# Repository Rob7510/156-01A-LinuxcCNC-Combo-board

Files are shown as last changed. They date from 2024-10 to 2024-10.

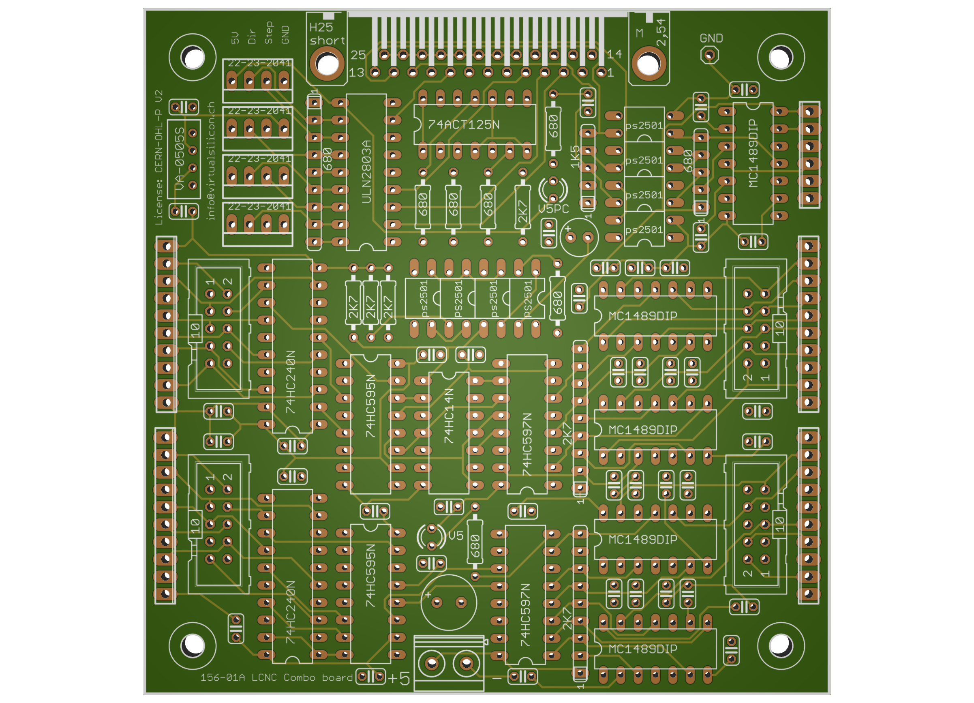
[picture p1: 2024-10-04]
image.png

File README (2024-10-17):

Note: First version, in test.

This board can drive in LinuxCNC a 3-axis CNC over a single printer port set to default(out/epp) mode,
and provides 4 (pin 10-13) + 16 signal inputs and 9 (pin 1-9) + 16 output signals using the integrated
LSRIO16 softwaare multiplexer.

The X, Y, Z axis and A (or two other signals instead of A) are not isolated from the PC,
they connect to stepper drivers that are normally floating.
The remaining 20 input and 16 output signals are electrically isolated from the PC.

Combo port example configuration:

Pin Output Signal
1   Enable
2   X step
3   X dir
4   Y step
5   Y dir
6   Z step
7   Z dir
8   Spindle  etc
9   Aux out
14  LSRIO16 output (fixed onboard)
16  LSRIO16 clock (fixed onboard)
17  LSRIO16 data latch (fixed onboard)

Pin Input signal
10  X home
11  Y home
12  Z home
13  Probe
15  LSRIO16 input (fixed onboard)

All other signals (eg limits, ext_estop, buttons, lights) can be handled by the 16 in and 16
output signals of the LSRIO16 multimplexer with a polling delay of max 300 msec.

LSRIO16 fixed signal connections 
RCLK   <- SRIO-DATA_LATCH (P17)
SRCLK  <- SRIO-CLOCK-OUTPUT (P16)
DT-OUT -> LSRIO-INPUT-STREAM (P15)
DT-IN  <- SRIO-OUTPUT-STREAM (P14)
SRLD = inverted RCLK

Test software to set outputs and read inputs: mx16_test.hal, mx16_test.xml

updated 2024-10-17

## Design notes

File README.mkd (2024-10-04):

This board is desiged to build a simple 3-axis CNC with this single 'combo' adapter.
The integrated LCNC LSRIO16 provides an additional 16 input and 16 output ports

The X, Y, Z axis and A or two other signals are not isolated, as they connect to stepper drivers.
The remainder of all I/O signals is electrically isolated from the PC.

Combo port example configuration:

Pin Output Signal
1   Enable
2   X step
3   X dir
4   Y step
5   Y dir
6   Z step
7   Z dir
8   Spindle  etc
9   Aux out
14  LSRIO16 output
16  LSRIO16 clock
17  LSRIO16 data latch

Pin Input signal
10  X home
11  Y home
12  Z home
13  Probe
15  LSRIO16 input

All other signals (limits, ext_estop)
can be handled by the 16 in and 16
output signals of the mux. (Polling
delay max 300 msec)

RCLK   <- SRIO-DATA_LATCH (P17)
SRCLK  <- SRIO-CLOCK-OUTPUT (P16)
DT-OUT -> LSRIO-INPUT-STREAM (P15)
DT-IN  <- SRIO-OUTPUT-STREAM (P14)
SRLD = inverted RCLK

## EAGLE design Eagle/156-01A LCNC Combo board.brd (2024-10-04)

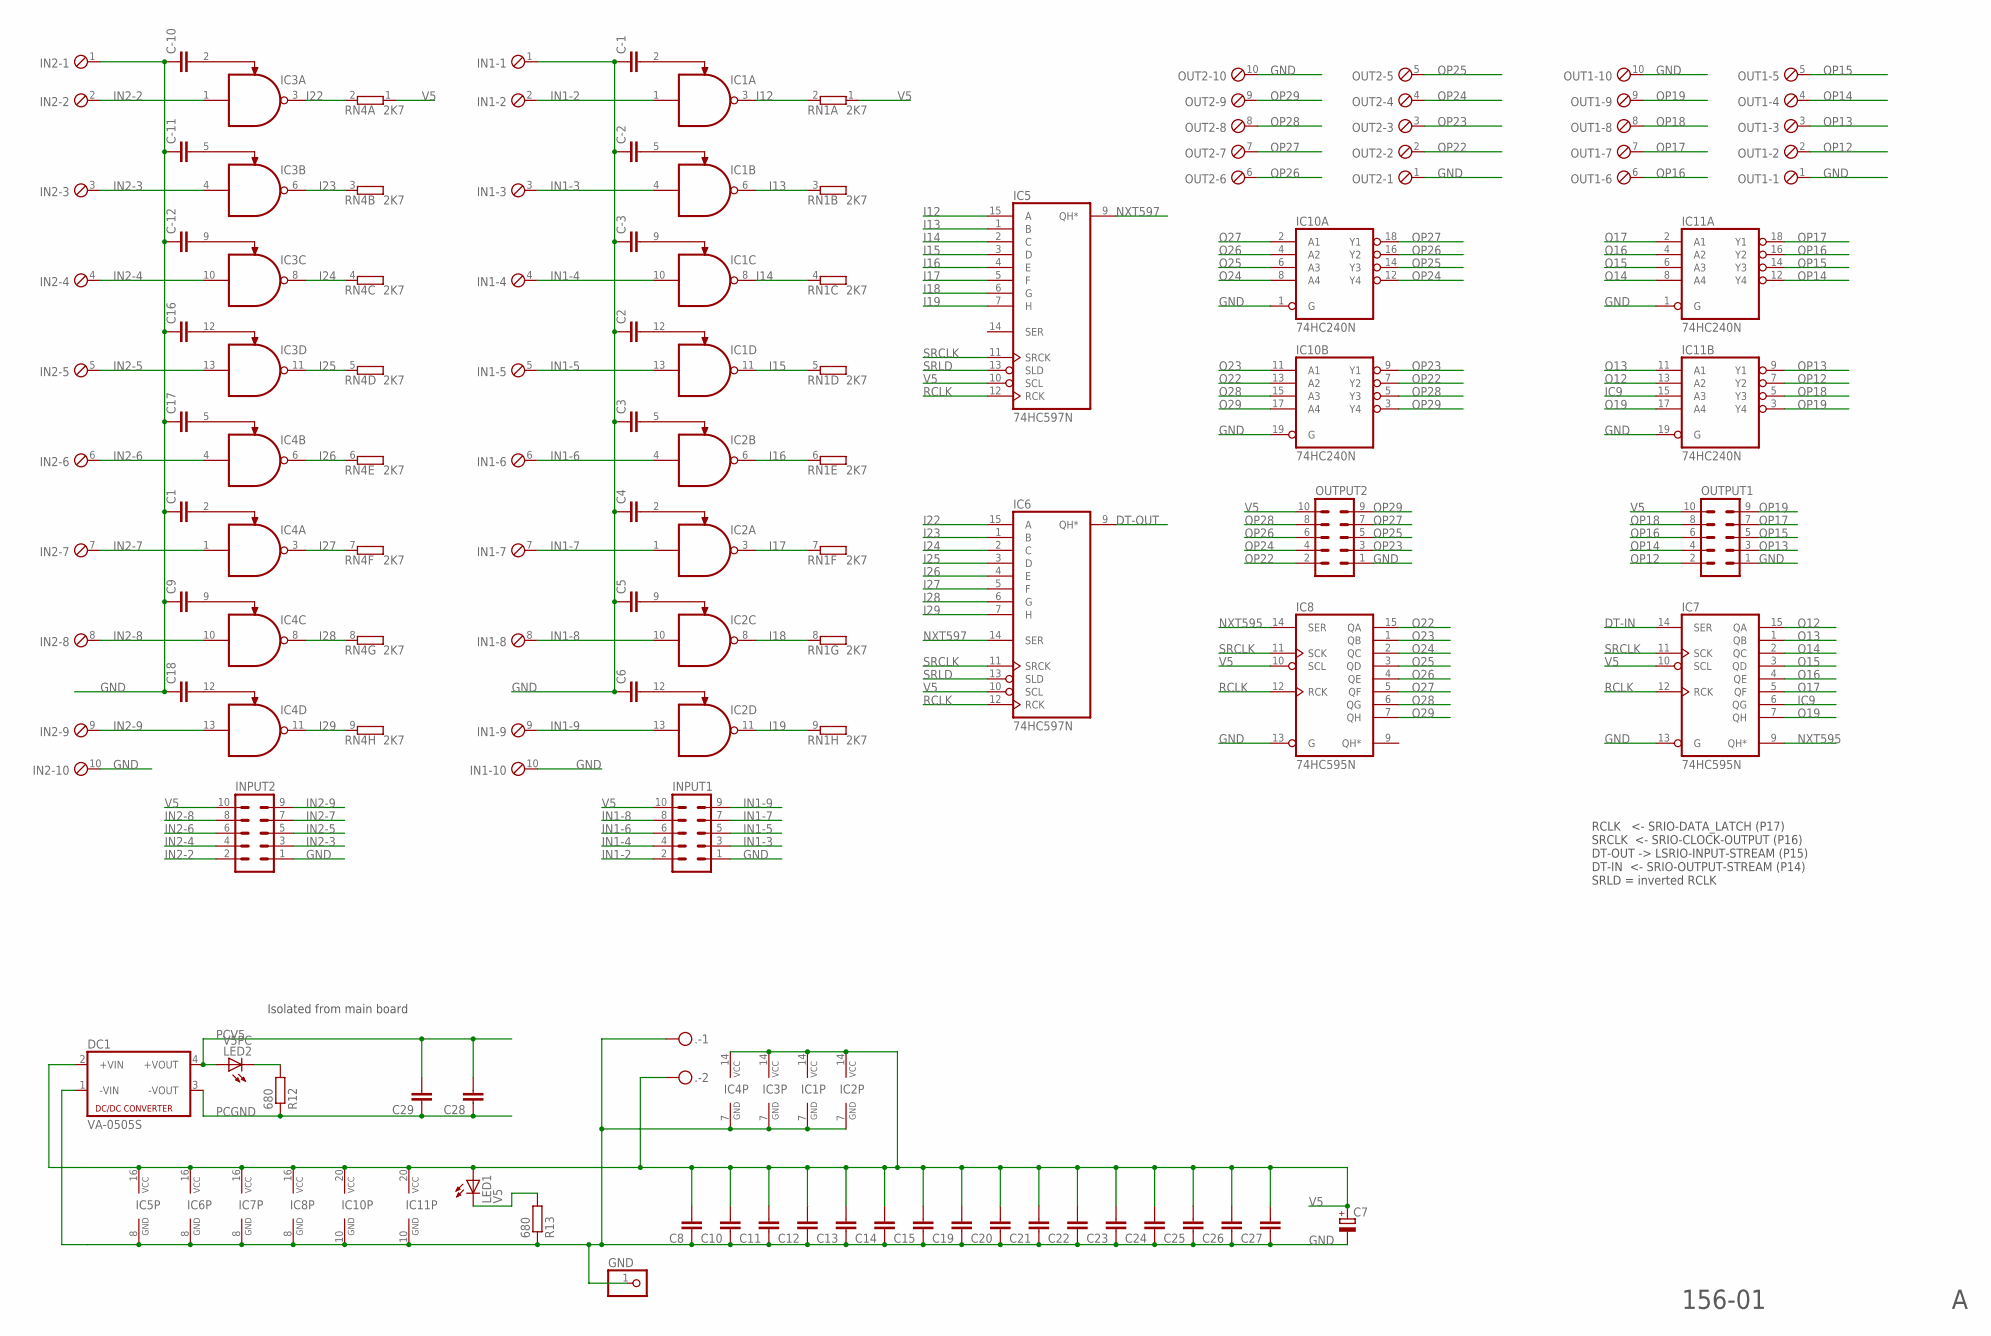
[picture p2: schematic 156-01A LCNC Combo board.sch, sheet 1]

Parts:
.: MKDSN1,5/2-5,08
C1, C2, C3, C4, C5, C6, C8, C9, C10, C11, C12, C13, C14, C15, C16, C17, C18, C19, C20, C21, C22, C23, C24, C25, C26, C27, C28, C29: C-EU025-024X044; C025-024X044
C7: CPOL-EUE3.5-8; E3,5-8
C-1, C-2, C-3, C-10, C-11, C-12: C-EU025-024X044; C025-024X044
DC1: VA-0505S; 4SIL
GND: PINHD-1X1; 1X01
IC1, IC2, IC3, IC4: MC1489DIP; DIL14
IC5, IC6: 74HC597N; DIL16
IC7, IC8: 74HC595N; DIL16
IC10, IC11: 74HC240N; DIL20
IN1, IN2: MPT10; 10POL254
INPUT1, INPUT2: ML10
LED1: V5; LED3MM
LED2: V5PC; LED3MM
OUT1, OUT2: MPT10; 10POL254
OUTPUT1, OUTPUT2: ML10
R12, R13: 680; 0207/10
RN1, RN4: 2K7; SIL9

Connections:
DT-IN: IC7.14 (SER); also elsewhere on the board
DT-OUT: IC6.9 (QH*); also elsewhere on the board
GND: ..1, C1.1, C2.1, C3.1, C4.1, C5.1, C6.1, C7.-, C8.1, C9.1, C10.1, C11.1, C12.1, C13.1, C14.1, C15.1, C16.1, C17.1, C18.1, C19.1, C20.1, C21.1, C22.1, C23.1, C24.1, C25.1, C26.1, C27.1, C-1.1, C-2.1, C-3.1, C-10.1, C-11.1, C-12.1, DC1.1 (-VIN), GND.1, IC1.7 (GND), IC2.7 (GND), IC3.7 (GND), IC4.7 (GND), IC5.8 (GND), IC6.8 (GND), IC7.8 (GND), IC7.13 (G), IC8.8 (GND), IC8.13 (G), IC10.1 (G), IC10.10 (GND), IC10.19 (G), IC11.1 (G), IC11.10 (GND), IC11.19 (G), IN1.1, IN1.10, IN2.1, IN2.10, INPUT1.1, INPUT2.1, OUT1.1, OUT1.10, OUT2.1, OUT2.10, OUTPUT1.1, OUTPUT2.1, R13.1; also elsewhere on the board
I12: IC1.3 (O), IC5.15 (A), RN1.2
I13: IC1.6 (O), IC5.1 (B), RN1.3 (2)
I14: IC1.8 (O), IC5.2 (C), RN1.4 (2)
I15: IC1.11 (O), IC5.3 (D), RN1.5 (2)
I16: IC2.6 (O), IC5.4 (E), RN1.6 (2)
I17: IC2.3 (O), IC5.5 (F), RN1.7 (2)
I18: IC2.8 (O), IC5.6 (G), RN1.8 (2)
I19: IC2.11 (O), IC5.7 (H), RN1.9 (2)
I22: IC3.3 (O), IC6.15 (A), RN4.2
I23: IC3.6 (O), IC6.1 (B), RN4.3 (2)
I24: IC3.8 (O), IC6.2 (C), RN4.4 (2)
I25: IC3.11 (O), IC6.3 (D), RN4.5 (2)
I26: IC4.6 (O), IC6.4 (E), RN4.6 (2)
I27: IC4.3 (O), IC6.5 (F), RN4.7 (2)
I28: IC4.8 (O), IC6.6 (G), RN4.8 (2)
I29: IC4.11 (O), IC6.7 (H), RN4.9 (2)
IC9: IC7.6 (QG), IC11.15 (A3)
IN1-2: IC1.1 (I0), IN1.2, INPUT1.2
IN1-3: IC1.4 (I0), IN1.3, INPUT1.3
IN1-4: IC1.10 (I0), IN1.4, INPUT1.4
IN1-5: IC1.13 (I0), IN1.5, INPUT1.5
IN1-6: IC2.4 (I0), IN1.6, INPUT1.6
IN1-7: IC2.1 (I0), IN1.7, INPUT1.7
IN1-8: IC2.10 (I0), IN1.8, INPUT1.8
IN1-9: IC2.13 (I0), IN1.9, INPUT1.9
IN2-2: IC3.1 (I0), IN2.2, INPUT2.2
IN2-3: IC3.4 (I0), IN2.3, INPUT2.3
IN2-4: IC3.10 (I0), IN2.4, INPUT2.4
IN2-5: IC3.13 (I0), IN2.5, INPUT2.5
IN2-6: IC4.4 (I0), IN2.6, INPUT2.6
IN2-7: IC4.1 (I0), IN2.7, INPUT2.7
IN2-8: IC4.10 (I0), IN2.8, INPUT2.8
IN2-9: IC4.13 (I0), IN2.9, INPUT2.9
unnamed: C-2.2, IC1.5 (I1)
unnamed: C-10.2, IC3.2 (I1)
unnamed: C17.2, IC4.5 (I1)
unnamed: C-3.2, IC1.9 (I1)
unnamed: C1.2, IC4.2 (I1)
unnamed: C9.2, IC4.9 (I1)
unnamed: C18.2, IC4.12 (I1)
unnamed: C2.2, IC1.12 (I1)
unnamed: C4.2, IC2.2 (I1)
unnamed: C5.2, IC2.9 (I1)
unnamed: C6.2, IC2.12 (I1)
unnamed: C-1.2, IC1.2 (I1)
unnamed: C3.2, IC2.5 (I1)
unnamed: LED2.K (C), R12.2
unnamed: LED1.K (C), R13.2
unnamed: C-11.2, IC3.5 (I1)
unnamed: C-12.2, IC3.9 (I1)
unnamed: C16.2, IC3.12 (I1)
NXT595: IC7.9 (QH*), IC8.14 (SER)
NXT597: IC5.9 (QH*), IC6.14 (SER)
O12: IC7.15 (QA), IC11.13 (A2)
O13: IC7.1 (QB), IC11.11 (A1)
O14: IC7.2 (QC), IC11.8 (A4)
O15: IC7.3 (QD), IC11.6 (A3)
O16: IC7.4 (QE), IC11.4 (A2)
O17: IC7.5 (QF), IC11.2 (A1)
O19: IC7.7 (QH), IC11.17 (A4)
O22: IC8.15 (QA), IC10.13 (A2)
O23: IC8.1 (QB), IC10.11 (A1)
O24: IC8.2 (QC), IC10.8 (A4)
O25: IC8.3 (QD), IC10.6 (A3)
O26: IC8.4 (QE), IC10.4 (A2)
O27: IC8.5 (QF), IC10.2 (A1)
O28: IC8.6 (QG), IC10.15 (A3)
O29: IC8.7 (QH), IC10.17 (A4)
OP12: IC11.7 (Y2), OUT1.2, OUTPUT1.2
OP13: IC11.9 (Y1), OUT1.3, OUTPUT1.3
OP14: IC11.12 (Y4), OUT1.4, OUTPUT1.4
OP15: IC11.14 (Y3), OUT1.5, OUTPUT1.5
OP16: IC11.16 (Y2), OUT1.6, OUTPUT1.6
OP17: IC11.18 (Y1), OUT1.7, OUTPUT1.7
OP18: IC11.5 (Y3), OUT1.8, OUTPUT1.8
OP19: IC11.3 (Y4), OUT1.9, OUTPUT1.9
OP22: IC10.7 (Y2), OUT2.2, OUTPUT2.2
OP23: IC10.9 (Y1), OUT2.3, OUTPUT2.3
OP24: IC10.12 (Y4), OUT2.4, OUTPUT2.4
OP25: IC10.14 (Y3), OUT2.5, OUTPUT2.5
OP26: IC10.16 (Y2), OUT2.6, OUTPUT2.6
OP27: IC10.18 (Y1), OUT2.7, OUTPUT2.7
OP28: IC10.5 (Y3), OUT2.8, OUTPUT2.8
OP29: IC10.3 (Y4), OUT2.9, OUTPUT2.9
PCGND: C28.1, C29.1, DC1.3 (-VOUT), R12.1; also elsewhere on the board
PCV5: C28.2, C29.2, DC1.4 (+VOUT), LED2.A; also elsewhere on the board
RCLK: IC5.12 (RCK), IC6.12 (RCK), IC7.12 (RCK), IC8.12 (RCK); also elsewhere on the board
SRCLK: IC5.11 (SRCK), IC6.11 (SRCK), IC7.11 (SCK), IC8.11 (SCK); also elsewhere on the board
SRLD: IC5.13 (SLD), IC6.13 (SLD); also elsewhere on the board
V5: ..2, C7.+, C8.2, C10.2, C11.2, C12.2, C13.2, C14.2, C15.2, C19.2, C20.2, C21.2, C22.2, C23.2, C24.2, C25.2, C26.2, C27.2, DC1.2 (+VIN), IC1.14 (VCC), IC2.14 (VCC), IC3.14 (VCC), IC4.14 (VCC), IC5.10 (SCL), IC5.16 (VCC), IC6.10 (SCL), IC6.16 (VCC), IC7.10 (SCL), IC7.16 (VCC), IC8.10 (SCL), IC8.16 (VCC), IC10.20 (VCC), IC11.20 (VCC), INPUT1.10, INPUT2.10, LED1.A, OUTPUT1.10, OUTPUT2.10, RN1.1, RN4.1; also elsewhere on the board

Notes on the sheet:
Isolated from main board
RCLK <- SRIO-DATA_LATCH (P17) SRCLK <- SRIO-CLOCK-OUTPUT (P16) DT-OUT -> LSRIO-INPUT-STREAM (P15) DT-IN <- SRIO-OUTPUT-STREAM (P14) SRLD = inverted RCLK
156-01

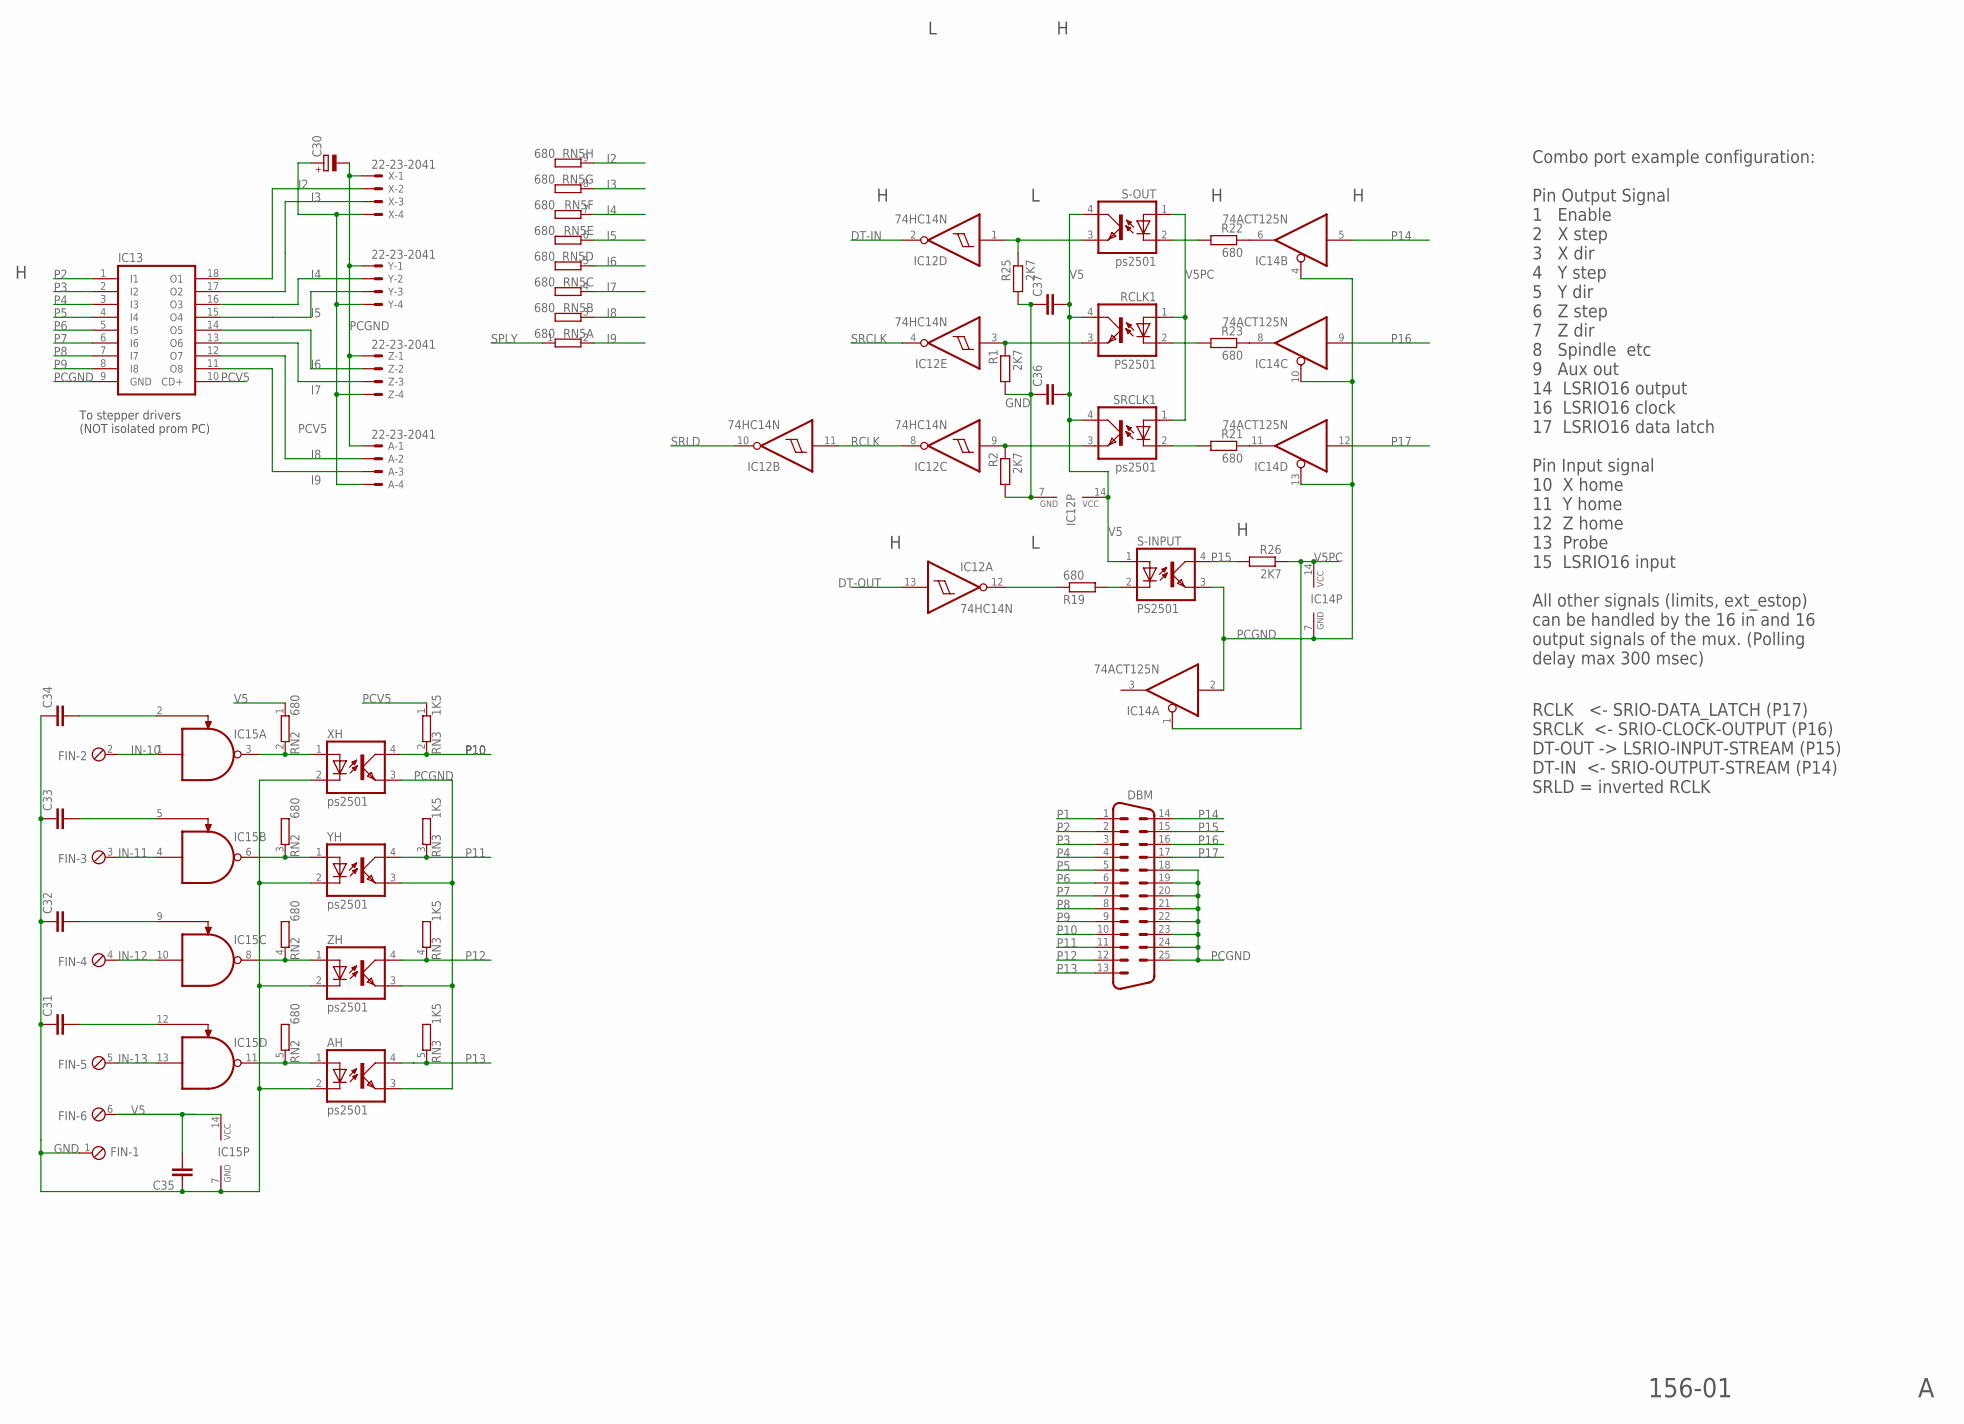
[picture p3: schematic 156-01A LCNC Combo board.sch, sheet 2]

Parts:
A: 22-23-2041
AH: ps2501; DIL04
C30: CPOL-EUE2.5-6; E2,5-6
C31, C32, C33, C34, C35, C36, C37: C-EU025-024X044; C025-024X044
DBM: M25HP
FIN: MPT6; 6POL254
IC12: 74HC14N; DIL14
IC13: ULN2803A; DIL18
IC14: 74ACT125N; DIL14
IC15: MC1489DIP; DIL14
R1, R2, R25, R26: 2K7; 0207/10
R19, R21, R22, R23: 680; 0207/10
RCLK1: PS2501; DIL04
RN2: 680; SIL5
RN3: 1K5; SIL5
RN5: 680; SIL9
S-INPUT: PS2501; DIL04
S-OUT: ps2501; DIL04
SRCLK1: ps2501; DIL04
X: 22-23-2041
XH: ps2501; DIL04
Y: 22-23-2041
YH: ps2501; DIL04
Z: 22-23-2041
ZH: ps2501; DIL04

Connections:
DT-IN: IC12.2 (O); also elsewhere on the board
DT-OUT: IC12.13 (I); also elsewhere on the board
GND: AH.2 (C), C31.1, C32.1, C33.1, C34.1, C35.1, C36.1, C37.1, FIN.1, IC12.7 (GND), IC15.7 (GND), R1.2, R2.2, R25.2, XH.2 (C), YH.2 (C), ZH.2 (C); also elsewhere on the board
I2: IC13.18 (O1), RN5.9 (2), X.2
I3: IC13.17 (O2), RN5.8 (2), X.3
I4: IC13.16 (O3), RN5.7 (2), Y.2
I5: IC13.15 (O4), RN5.6 (2), Y.3
I6: IC13.14 (O5), RN5.5 (2), Z.2
I7: IC13.13 (O6), RN5.4 (2), Z.3
I8: A.2, IC13.12 (O7), RN5.3 (2)
I9: A.3, IC13.11 (O8), RN5.2
IN-10: FIN.2, IC15.1 (I0)
IN-11: FIN.3, IC15.4 (I0)
IN-12: FIN.4, IC15.10 (I0)
IN-13: FIN.5, IC15.13 (I0)
unnamed: IC15.3 (O), RN2.2, XH.1 (A)
unnamed: IC14.6 (O), R22.1
unnamed: IC15.8 (O), RN2.4 (2), ZH.1 (A)
unnamed: AH.1 (A), IC15.11 (O), RN2.5 (2)
unnamed: C33.2, IC15.5 (I1)
unnamed: C34.2, IC15.2 (I1)
unnamed: C32.2, IC15.9 (I1)
unnamed: C31.2, IC15.12 (I1)
unnamed: IC15.6 (O), RN2.3 (2), YH.1 (A)
unnamed: R22.2, S-OUT.2 (C)
unnamed: IC12.3 (I), R1.1, RCLK1.3 (EMIT)
unnamed: R23.2, RCLK1.2 (C)
unnamed: IC12.1 (I), R25.1, S-OUT.3 (EMIT)
unnamed: IC12.9 (I), R2.1, SRCLK1.3 (EMIT)
unnamed: R21.2, SRCLK1.2 (C)
unnamed: IC12.12 (O), R19.1
unnamed: IC14.11 (O), R21.1
unnamed: IC14.8 (O), R23.1
unnamed: R19.2, S-INPUT.2 (C)
P1: DBM.1
P2: DBM.2, IC13.1 (I1)
P3: DBM.3, IC13.2 (I2)
P4: DBM.4, IC13.3 (I3)
P5: DBM.5, IC13.4 (I4)
P6: DBM.6, IC13.5 (I5)
P7: DBM.7, IC13.6 (I6)
P8: DBM.8, IC13.7 (I7)
P9: DBM.9, IC13.8 (I8)
P10: DBM.10, RN3.2, XH.4 (COL)
P11: DBM.11, RN3.3 (2), YH.4 (COL)
P12: DBM.12, RN3.4 (2), ZH.4 (COL)
P13: AH.4 (COL), DBM.13, RN3.5 (2)
P14: DBM.14, IC14.5 (I)
P15: DBM.15, R26.2, S-INPUT.4 (COL)
P16: DBM.16, IC14.9 (I)
P17: DBM.17, IC14.12 (I)
PCGND: A.1, AH.3 (EMIT), C30.-, DBM.18, DBM.19, DBM.20, DBM.21, DBM.22, DBM.23, DBM.24, DBM.25, IC13.9 (GND), IC14.2 (I), IC14.4 (OE), IC14.7 (GND), IC14.10 (OE), IC14.13 (OE), S-INPUT.3 (EMIT), X.1, XH.3 (EMIT), Y.1, YH.3 (EMIT), Z.1, ZH.3 (EMIT); also elsewhere on the board
PCV5: A.4, C30.+, IC13.10 (CD+), RN3.1, X.4, Y.4, Z.4; also elsewhere on the board
RCLK: IC12.8 (O), IC12.11 (I); also elsewhere on the board
SPLY: RN5.1
SRCLK: IC12.4 (O); also elsewhere on the board
SRLD: IC12.10 (O); also elsewhere on the board
V5: C35.2, C36.2, C37.2, FIN.6, IC12.14 (VCC), IC15.14 (VCC), RCLK1.4 (COL), RN2.1, S-INPUT.1 (A), S-OUT.4 (COL), SRCLK1.4 (COL); also elsewhere on the board
V5PC: IC14.1 (OE), IC14.14 (VCC), R26.1, RCLK1.1 (A), S-OUT.1 (A), SRCLK1.1 (A)

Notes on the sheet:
Combo port example configuration: Pin Output Signal 1 Enable 2 X step 3 X dir 4 Y step 5 Y dir 6 Z step 7 Z dir 8 Spindle etc 9 Aux out 14 LSRIO16 output 16 LSRIO16 clock 17 LSRIO16 data latch Pin Input signal 10 X home 11 Y home 12 Z home 13 Probe 15 LSRIO16 input All other signals (limits, ext_es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
To stepper drivers (NOT isolated prom PC)
RCLK <- SRIO-DATA_LATCH (P17) SRCLK <- SRIO-CLOCK-OUTPUT (P16) DT-OUT -> LSRIO-INPUT-STREAM (P15) DT-IN <- SRIO-OUTPUT-STREAM (P14) SRLD = inverted RCLK
156-01

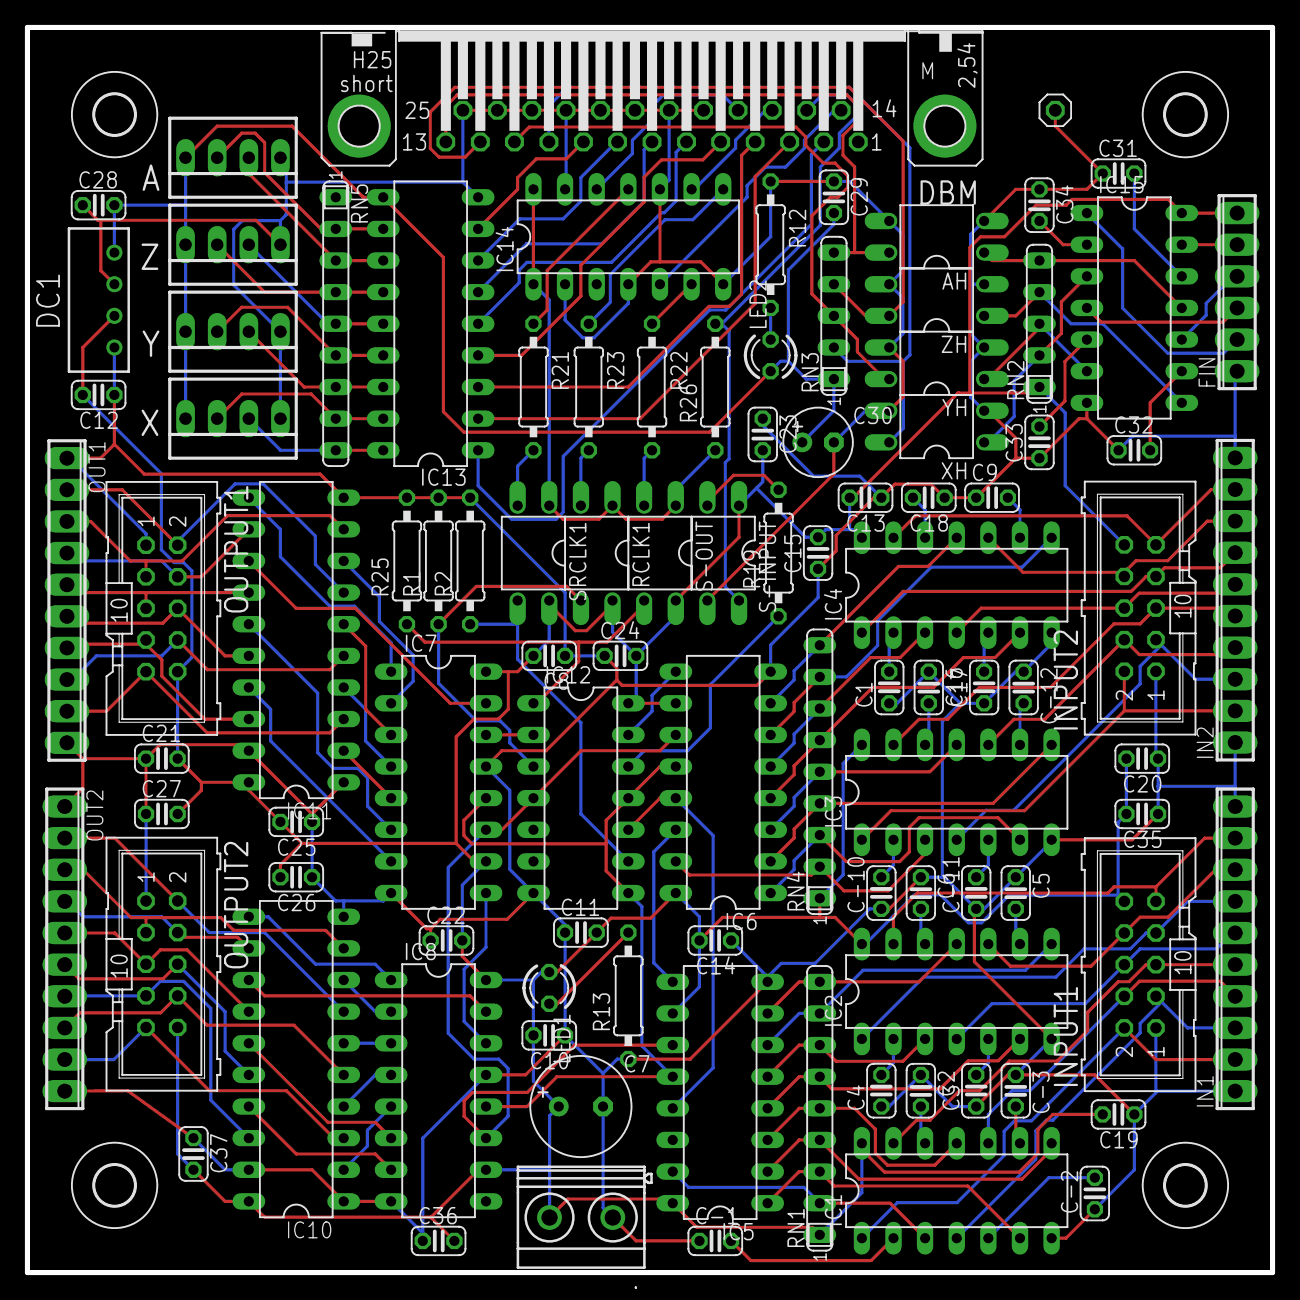
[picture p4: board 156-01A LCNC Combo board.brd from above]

Board: 2 copper layers, 100.0 x 100.0 mm, 103 parts (0 on the bottom side), 141 nets.

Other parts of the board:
U$1, U$2, U$3, U$4: 3,2

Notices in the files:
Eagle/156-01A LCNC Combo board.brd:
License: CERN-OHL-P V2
